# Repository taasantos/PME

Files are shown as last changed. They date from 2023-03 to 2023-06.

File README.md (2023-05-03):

# O meu repositório

## PME_5_ano - Dimensionamento de uma Ladder Hoist

### gear_defenition

Este ficheiro possui o código base para o dimensionamento de engrenagens.

**V3**

	- Equação dos módulos corrigida e módulos estão agora corretos

**V4**

	- Velocidades dos diferentes níveis corrigidaa
	- Alteração dos materiais para tentar manter os módulos abaixo de 6
	- Alteração do numero de dentes
	- Alteração do fator de condução
	- Acréscimo do cálculo do erro da velocidade de saida tendo em consideração a norma DIN 804

Estas alterações mudaram os valores todos das engrenagens e precisam de ser atualizados no relatório!!

**V5**

	- Alteração do diametro do tambor
	- Alteração da relação de transmissão o que altera o resto dos valores todos

**V6**

	- Alteração do diametro do tambor
	- Alteração dos angulos de engrenamento
	- Alteração do número de dentes
	- Alteração do módulo normalizado
	- Alteração do material da ultima engrenagem

---

Para verem os parametros das rodas e dos pinhões usar:

pinhao(nº de engrenamento)

roda(nº de engrenamento)

### problem_variables

Este ficheiro possui a defenição das variáveis do problema 

### gear_shafts

Este ficheiro possui o dimensionamento dos veios de transmisssão

**V2**

	- Calculo das forças de engrenamento
	- Calculo das forças exercidas nos veios
	- Dimensionamento do X0 Y0, X Y.
	- Cálculo dos Ps e c0 e c
	- Determinação dos rolamentos

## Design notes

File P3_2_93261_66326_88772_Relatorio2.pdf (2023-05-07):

# 2022/2023 Escada Elevatória Trabalho 2

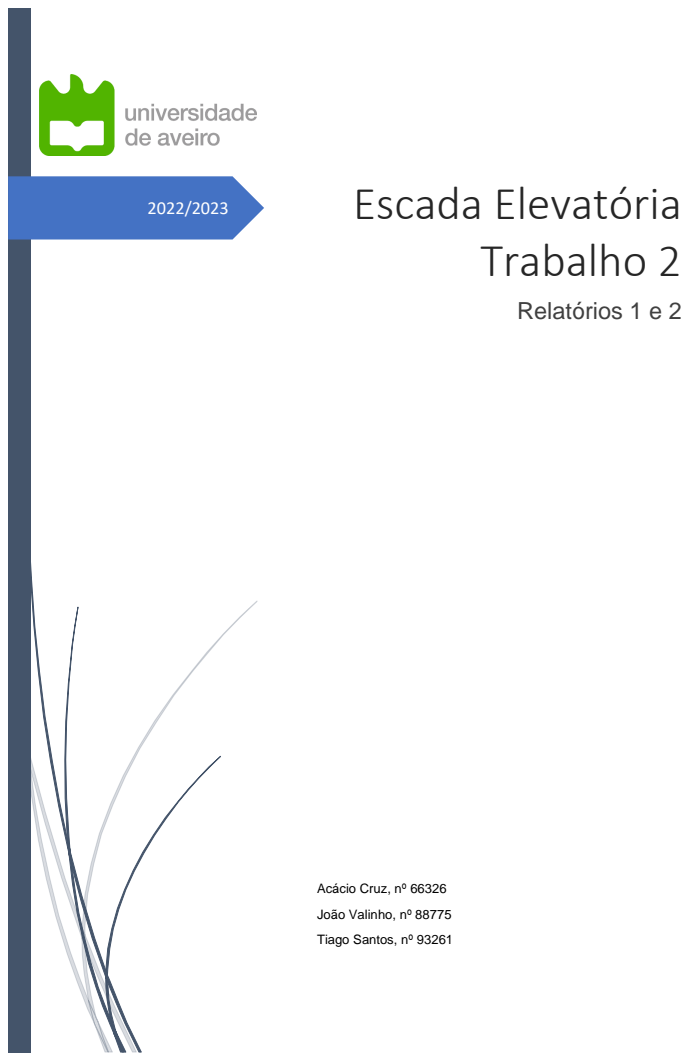
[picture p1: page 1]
Relatórios 1 e 2

Acácio Cruz, nº 66326

João Valinho, nº 88775

Tiago Santos, nº 93261

## Índice

Relatório 1

1. Introdução
1.1. Objetivo do projeto e enunciado
Uma escada elevatória é um mecanismo para transporte de carga de um nível de altura para outro. Ela é composta por uma plataforma elevatória montada em uma estrutura vertical que é acionada por um sistema elétrico. São geralmente usadas para fornecer acesso de materiais aos telhados de edifícios, movendo-se verticalmente ou numa inclinação.

O presente projeto visa, no âmbito da unidade curricular de Projeto de Máquinas e Estruturas, projetar uma escada elevatória para o transporte de painéis solares térmicos e fotovoltaicos a serem instalados em telhados. Assim sendo, inicialmente, traçar o sistema mecânico e elevatório. Consequentemente elevar o nosso conhecimento através da interligação de competências previamente adquiridas.

Será aplicado a este mecanismo, um redutor de velocidades proporcionando, assim, a diminuição da velocidade de um motor elétrico, mantendo a transmissão da potência constante de um motor, e aumento do binário, assegurando o transporte de painéis solares ao longo de uma escada elevatória.

Na primeira parte deste relatório, mostra-se um cronograma referente ao planeamento, apresenta-se o caderno de encargos do mecanismo a projetar e a análise a uma solução de mercado similar à do projeto em causa.

A seguir, é realizado uma descrição do mecanismo que a ser projetado, onde se indica os requisitos impostos de acordo com um enunciado e os que foram definidos pelos elementos do grupo imprescindíveis para o dimensionamento dos componentes mecânicos. Além disso, mostra-se a comparação de uma solução de mercado com uma aplicação similar à que se está a elaborar.

Posteriormente, é apresentado o método sequencial de todos os cálculos inerentes para dimensionar cada componente, compreendendo definições e condições teóricas e as relações de dependência entre a determinação das proporções de cada um, como por exemplo, os diâmetros do cabo e do tambor e das potências entre o redutor de velocidades (de eixos paralelos com veio de entrada e saída coaxiais, que inclui rodas dentadas helicoidais) e o motor que o aciona. Após cada componente dimensionado, mostra-se e discute-se os dados obtidos.

Por fim, expõe-se quer as considerações e verificações finais quer os valores obtidos mais relevantes a fim de se atingir o objetivo deste primeiro relatório.

1.2. Planeamento
Procurou-se reunir todos os membros do grupo semanalmente e em cada reunião, discutir as etapas do projeto de forma clara e específica. De modo a identificar os recursos, quer pessoais quer temporais, necessários para o cumprimento de cada tarefa, definiram-se áreas de especialização para cada elemento. Além disso, recorreu-se à criação de um cronograma detalhado (diagrama de Gantt) para o projeto, que inclui prazos e tarefas específicas para cada membro do grupo. Na figura 1, observa-se detalhadamente o trabalho desenvolvido ao longo das primeiras 5 semanas.

Figura 1 – Diagrama de Gantt.

2. Caderno de encargos do mecanismo
2.1. Descrição do mecanismo a projetar
O sistema mecânico é constituído por um motor freio acoplado a uma caixa redutora que inclui três pares de engrenagens de dentado helicoidal, para além de estar fixado a um tambor. Para o sistema elevatório, o cabo terá de ser capaz de efetuar a subida de cargas até à altura mencionada a seguir.

O dimensionamento destes componentes teve em conta os dados fornecidos pelo enunciado:

- Capacidade de carga/elevação: 250 kg;
- Área para elevação: 0,5 m x 1 m;
- Capacidade de elevação: 12 m;
- Velocidade de elevação: 35 m/min;

Além disso, considerou-se outros parâmetros e/ou características inerentes aos componentes projetados:

- Caixa redutoras de 3 velocidades para aplicar em elevação de carga;
- Estrutura dos grupos redutores é 2x1;
- Acionamento é feito por um motor freio;
- Par de engrenagens- 1º em aço de carbono C45, 2º em carbono temperado 33Mn5, 3º em aço ligado temperado 34NiCrMo6;
- Seleção de velocidade por um único manípulo;
- Potência de entrada – 1,39 kW;
- Velocidade de entrada – 1430 rpm;
- Velocidade de saída– 40,53 rpm.
3. Benchmarking – Easy Big WH-KI
O Easy Big WH-KI da GGR Group é um guindaste de escada projetado para transportar materiais de construção e equipamentos para um local de trabalho em alturas elevadas. Ele é montado em uma escada ou andaime, e o material ou equipamento é levantado por meio de uma polia conectada a um motor elétrico. Este produto é frequentemente usado em espaços de obras. [3]

Abaixo estão alguns pontos fortes e fracos do produto:

Pontos fortes:

- Fácil montagem e desmontagem.
Project Start Date | Display Week | 1
Project Name
| 13 | 14 | 15 | 16 | 17 | 18 | 19 | 20 | 21 | 22 | 23 | 24 | 25 | 26 | 27 | 28 | 1 | 2 | 3 | 4 | 5 | 6 | 7 | 8 | 9 | 10 | 11 | 12 | 13 | 14 | 15 | 16 | 17 | 18 | 19
WBS | TASK | LEAD | START | END | DAYS | %
DONE

WORK
DAYS | M | T | W | T | F | S | S | M | T | W | T | F | S | S | M | T | W | T | F | S | S | M | T | W | T | F | S | S | M | T | W | T | F | S | S
1 | Relatório 1 | - | -
1.1 | Marcação das reuniões semanais | Todos | sex 2/17/23 | sex 2/17/23 | 1 | 100% | 1
1.2 | Planificação das tarefas | Todos | sex 2/17/23 | sex 2/17/23 | 1 | 100% | 1
1.3 | Diagrama de Gantt | JV | sex 2/17/23 | dom 2/19/23 | 3 | 100% | 1
1.4 | Dimensionamento em Matlab | TS | sáb 2/18/23 | sex 3/10/23 | 21 | 100% | 15
1.4.1 | Criar Script de cálculo | TS | sáb 2/18/23 | qui 2/23/23 | 6 | 100% | 4
1.4.2 | Dimensionamento das
engrenagens
TS | sex 2/24/23 | qua 3/01/23 | 6 | 100% | 4
1.4.3 | Otimização das engrenagens | TS | sáb 3/04/23 | qua 3/08/23 | 5 | 100% | 3
1.4.4 | Verificações velocidades de saída | TS | qua 3/08/23 | qui 3/09/23 | 2 | 100% | 2
1.4.4 | Verificação da razão de condução | TS | qui 3/09/23 | sex 3/10/23 | 2 | 100% | 2
1.5 | Dimensionamento e seleção dos
restantes componentes | AC,JV | seg 2/20/23 | sex 3/10/23 | 19 | 100% | 15
1.5.1 | Cabo | AC,JV | seg 2/20/23 | sáb 2/25/23 | 6 | 100% | 5
1.5.2 | Tambor | AC,JV | sáb 2/25/23 | qui 3/02/23 | 6 | 100% | 4
1.5.3 | Motor | AC,JV | sex 3/03/23 | dom 3/05/23 | 3 | 100% | 1
1.5.4 | Verifcação e correção dos
cálculos | AC,JV | sex 3/03/23 | sex 3/10/23 | 8 | 100% | 6
1.6 | Desenho esquemas cinemáticos | AC | qua 3/01/23 | seg 3/13/23 | 13 | 100% | 9
1.6.1 | Realização do esboço
cinemático | AC | sex 3/03/23 | sáb 3/04/23 | 2 | 100% | 1
1.6.2 | Realização do esquema
cinemático final | AC | dom 3/12/23 | seg 3/13/23 | 2 | 100% | 1
1.7 | Produção do Relatório | JV | sex 3/03/23 | sex 3/17/23 | 15 | 100% | 11
1.7.1 | Criação da estrutura do
documento | JV | sex 3/03/23 | dom 3/05/23 | 3 | 100% | 1
1.7.2 | Escrita do documento | Todos | dom 3/05/23 | sex 3/17/23 | 13 | 100% | 10

Week 4

6 mar 2023 | 13 mar 2023 Week 5
Ladder Hoist
2/17/2023 (sexta-feira) | Semana 1 | Semana 2
| 13 fev 2023 | 20 fev 2023

Semana 3
27 fev 2023

- Capacidade máxima de carga de 250 kg.
- Possibilidade de elevação de materiais até 24 metros de altura, com articulação.
- Velocidade de elevação ajustável.
- Sistema de freio automático de segurança.
- Adequado para locais de construção em áreas urbanas onde o espaço é limitado e não é possível usar guindastes maiores.
- Redução dos riscos de lesões nos trabalhadores que realizam a elevação manual de materiais.

Pontos fracos:

- Capacidade limitada de carga em comparação com guindastes maiores.
- A mobilidade é restrita a locais onde uma escada ou andaime podem ser utilizados para a sua instalação.
- A operação do guindaste requer treinamento e habilidade para garantir a segurança dos trabalhadores e evitar danos aos materiais ou equipamentos transportados.
- Custo de aluguer ou compra pode ser maior do que o de outras soluções de elevação de materiais.

Em resumo, o Easy Big WH-KI pode ser uma opção eficiente e segura para a elevação de materiais em locais de construção em áreas urbanas ou onde não é possível usar guindastes maiores, desde que seja operado adequadamente e respeitando as suas limitações de carga e mobilidade.

Em comparação com esse produto concorrente, o mecanismo projetado tem uma capacidade máxima de carga semelhante, mas uma altura máxima de elevação menor.

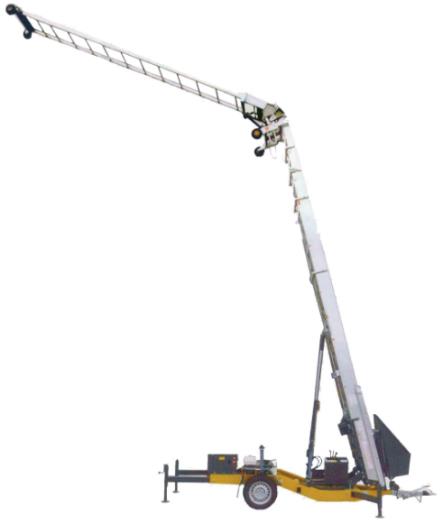
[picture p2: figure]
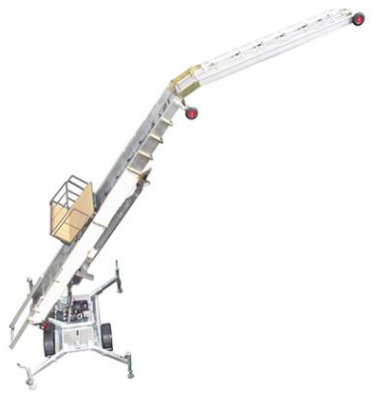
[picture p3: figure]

4. Dimensionamento e seleção dos componentes mecânicos
4.1. Cabo
O primeiro componente a ser dimensionado foi o cabo de aço. As classes e tipos de cabos de aço selecionados para o estudo serão apresentados na tabela 1, juntamente com as características imprescindíveis para os cálculos retiradas de [2].

A fim de se aumentar o tempo de vida deste componente e este não se romper, utilizou-se um fator de segurança (fs) de 5 para guinchos, de acordo com a tabela 6.27 de [2].

Figura 2 – Imagem ilustrativa do Easy Big WH-KI.

Tabela 1 – Exemplos cabos de aço

Tipo | Classe | Fator de contrução (f) | Fator para diâmetro mínimo/recomendado do tambor (ft) | Carga de rutura mínima [kN] | Tensão de rotura [MPa]
1x7 | Cordão | 0,596 | - | 13,7 | 1570
1x19 | | 0,58 | - | 13,2
6x19 | Seale | 0,395 | 34/51 | 27 | 1770
6x25 | Filler, WS | 0,405 | 26/39 | 41
6x36 | | | 23/35 | 35,7 (1*) | -

1* - O valor de carga de rutura mínima foi pesquisado em [2].

Primeiramente, definiu-se o comprimento do cabo através da equação (1), sendo a altura máxima 12 metros.

Lc = 2 × Hmáx
(1)
Lc = 2 × 12 = 24
- Lc – comprimento do cabo [m]
- Hmáx – altura máxima [m]

Adicionou-se 2 metros ao comprimento final, obtendo-se então 26 metros de comprimento do cabo, visto que o diâmetro do tambor é 0,305 metros, conta-se com mais 2 polias do mesmo diâmetro, o que perfaz um aumento de 1,9 metros, aproximadamente.
De seguida, procedeu-se à determinação da área transversal do cabo e do peso carga que o cabo tem de suportar, desprezando as forças de atrito, a partir das equações (2) e (3), respetivamente. Assim, a expressão (4) calcula a pressão nessa área. Os valores apresentados referem-se ao cabo que foi escolhido, sublinhado a verde, ou seja, para os outros cabos aplicou-se o mesmo procedimento.

Ac =

Øc

2 × π
4 | (2)

Ac =

0,008 ² × π
4

= 5,027 ∗ 10⁻⁵

- Ac – área transversal do cabo [m² ]
- Øc – diâmetro do cabo [m]
F = m × g | (3)

P = 250 × 9,81 = 2452,50

- F – força aplicada ao cabo [N]
- g – constante gravitacional = 9,81 [m/s² ]
- m – massa da carga [kg]

σ =

F
Ac | (4)

σ =

2452,50
5,027 ∗ 10⁻⁵ = 49 Mpa

- F – força aplicada ao cabo [N]
- Ac – área transversal do cabo [m²
]
- σ – tensão axial no cabo [MPa]

Depois, mediu-se a deformação elástica do cabo pela lei de Hooke com a equação (5). A área metálica efetiva do cabo foi estimada com recorrendo à equação (6), sendo o módulo de Young para cabos de aço é 200 GPa.

ΔL =

F × L
Am × E | (5)

ΔL =

2452,5 × 26
9,50 × 10⁻⁶ × 200 × 10⁹ = 0,17 m
- F – força aplicada ao cabo [N]
- Am – área metálica efetiva do cabo [m² ]
- ∆L– alongamento do cabo [m]
- E – módulo de elasticidade [GPa]
- Lc – comprimento do cabo [m]

Am = f × Øc

2 | (6)

Am = 0,38 × 0,005² = 9,56 × 10⁻⁶ m²

- Am – área metálica efetiva do cabo [m² ]
- Øc – diâmetro do cabo [m]
- f - fator de construção [adimensional]

Por fim, aplicando a equação (7), determinou-se os valores mínimo e recomendado para o diâmetro do tambor, deve estar preferencialmente compreendido no intervalo [0,238; 0,476] metros. Deste modo, é permitido fazer a comparação dos resultados obtidos para cada um dos cabos na tabela 2.

Øt = ft × Øc | (7)

Øt,mín = 42 × 0,005 = 0,21 m

Øt,rec = 72 × 0,014 = 0,36 m

- Øt – diâmetro do tambor [m]
- Øc – diâmetro do cabo [m]
- ft – Fator para o diâmetro mínimo/recomendado do tambor [adimensional]

Tabela 2 - Valores obtidos para selecionar o cabo.

Após o seu dimensionamento, o cabo selecionado é do tipo 6x7, da classe CF, fornecido pela Luiz Godinho. [3]

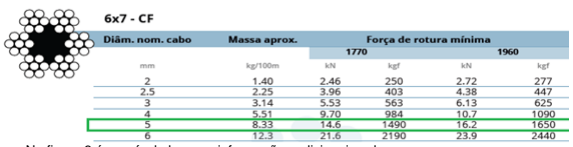
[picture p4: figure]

Na figura 3 é possível observar informações adicionais sobre o mesmo.

4.2. Tambor
A partir da determinação do comprimento do cabo, pode-se utilizar esse valor para calcular o número de voltas do tambor, mas antes deve-se obter o seu perímetro, recorrendo aos valores dos diâmetros recomendado e mínimo, através das equações (8) e (9).
Pt = Øt × π | (8)

Pt,d rec = 0,36 × π = 1,13 m

Pt,d mín = 0,21 × π = 0,659 m

- Pt –perímetro do tambor [m]
- Øt – diâmetro do tambor [m]

Nvoltas =

Lc
Pt

(9)

Nvoltas,d rec =

26
1,13 = 23

Nvoltas,d mín =

26
0,659 = 39
- Nvoltas – número de voltas [adimensional]
- Pt –perímetro do tambor [m]
- Lc – comprimento do cabo [m]

Posteriormente, fez-se uma pesquisa em [4], e acrescentou-se o cálculo dos valores necessários para o dimensionamento do tambor.
Deste modo, determinou-se 4 parâmetros da ranhura do cabo que permitem definir o comprimento do tambor, sendo mencionados a seguir, bem como se apresenta as respetivas equações (10 a 13). Os resultados obtidos podem ser observados na tabela 3, tal como na figura 4 está ilustrado o desenho técnico de um tambor com esses parâmetros.
A = 1,08 × Øc | (10)

A = 1,08 × 0,005 = 0,0054 m

B = 1,06 × Øc | (11)

B = 1,06 × 0,005 = 0,0053 m

C = 0,3 × Øc | (12)

C = 0,3 × 0,005 = 0,0015 m

R = 0,15 × Øc | (13)

R = 0,15 × 0,005 = 0,00075 m

- A – elevação da ranhura [m]
- B – diâmetro da ranhura [m]
- C – profundidade da ranhura [m]
- D – raio superior [m]
- Øc – diâmetro do cabo [m]

Tabela 3 - Parâmetros associados às ranhuras do cabo.

Parâmetros | Resultado | Unidades
A | 0,005 | m
B | 0,005 | m
C | 0,002 | m
R | 0,001 | m

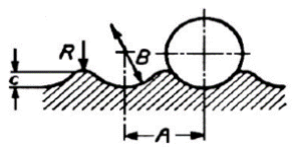
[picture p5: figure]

Após o cálculo da elevação da ranhura (A), deu-se o cálculo do comprimento do tambor através da equação (14). Os valores obtidos para o comprimento do tambor mínimo e recomendado foi 0,24 e 0,35 metros, respetivamente. A figura 5 mostra qual a dimensão do tambor que está a ser determinada.

Lt = (Nvoltas × A)+ Øc
(14)

Lt,d rec = (23 × 0,005) + 0,005 = 0,12

Lt,d mín = (39 × 0,005) + 0,005 = 0,20

- A – elevação da ranhura [m]
- Nvoltas – número de voltas [adimensional]
- Lt – comprimento do tambor [m]
- Øc – diâmetro do cabo [m]

Figura 3 – Localização dos parâmetros A, B, C, D associados à ranhura do cabo num desenho técnico.

Figura 4 – Visualização do comprimento do tambor.

Por fim, determinou-se a distância mínima entre o tambor e a roldana. Tendo em conta que o nosso cabo tem ranhuras, recorreu-se à equação (15), previamente definida, para se obter essa distância.

O ângulo de desvio de cabos de aço (β) é 2°.

O resultado obtido para os comprimentos do tambor mínimo e recomendado foram 5,3 metros e 3,6 metros, respetivamente. Verifica-se na figura 6 um desenho representativo do mesmo.

Lmín = 15 × Lt
(15)

Lmín,d rec = 15 × 0,12 = 1,8

Lmín,d mín = 15 × 0,20 = 3

- Lmín– distância mínima entre o tambor e a polia [m]
- Lt – comprimento do tambor [m]

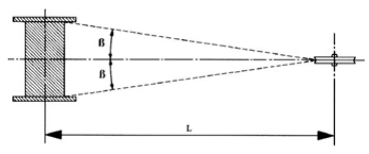
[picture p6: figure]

No seguimento das necessidades encontradas, no mercado propõe-se a seguinte solução na Tabela 4, cujo fornecedor é a Eletrolift. [5]

Tabela 4 – Comparação entre os valores obtidos e os do tambor.

Øt [m] | Pt [m] | Nvoltas | Lt [m] | Lmín [m]
Intervalo aceitável | [0,21; 0,36] | [1,13; 0,659] | [23; 39] | [0,12; 0,20] | [1,8; 3]
Modelo M-303-P2 | 0,3048 | 0,958 | 23 | 0,22 | 3,2
4.3. Motor
As características que se teve em conta para a seleção do motor foram este ser elétrico, a sua potência e a sua velocidade de rotação.

Deste modo, seguiu-se o seguinte procedimento de cálculo: força aplicada (Peso) quando a escada é vertical e o torque do motor quando a distância do eixo do tambor é igual ao seu raio (metade do diâmetro), recorrendo às equações (3) e (16).

τm = F ×

∅t
2

(16)

Tm = 2452,5 ×

0,360
2

= 441,45

- F– força aplicada ao cabo [m]
- Øt – diâmetro do tambor [m]
- Τm – torque do motor [Nm]

Após o cálculo do torque, obteve-se o valor da velocidade de saída do redutor com o intuito de definir a potência do motor, recorrendo às equações (17) e (18). Considerou-se a velocidade de elevação igual a 35 m/min, isto é, 0,583 m/s, aproximadamente.

Figura 6 – Distância entre o tambor e a polia e o ângulo de desvio de cabos de aço.

- ωsaída − velocidade de saída do redutor [rpm]
- velev – velocidade de elevação [m/s]
- Øt – diâmetro do tambor [m]
- ωsaída − velocidade de saída do redutor [rpm]
- P – potência do motor [kW]
- Τm – torque do motor [Nm]

Assim sendo, escolheu-se um trifásico IEC com freio DC fabricado pela Bernati, da série BCL. Algumas das características adicionais são as seguintes: [6]

- Potência do motor: 1,5 kW;
- Velocidade de rotação: 1500 rpm;
- Frequência (f): 50 Hz;
- 4 pólos;
- IP65: proteção total contra poeiras e contra jatos de água.

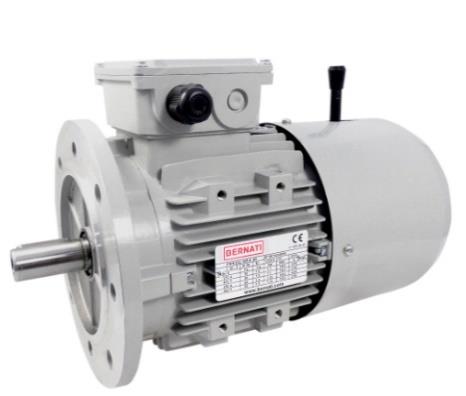
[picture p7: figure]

Figura 7 – Imagem do motor freio selecionado.

4.4. Engrenagens
4.4.1. Determinação do número de andares

Com a velocidade de saída do redutor determinada, estabeleceu-se o número de andares que o redutor terá, recorrendo à equação (19). Obteve-se um valor de 2,77, ou seja, 3 andares.

Nandares =

log10 (

ωentrada
ωsaída

)

log10(4)

(19)

Nandares =

log10 (

1430
30,93)

log10(4)

= 2,77 ≅ 3

- Nandares − número de andares [adimensional]
- ωentrada – velocidade de entrada [rpm]
- ωsaída − velocidade de saída do redutor [rpm]

ωsaída =

velev × 60
π × ∅t

(17)

ωsaída =

0,583 × 60
π × 0,360 = 30,93

P =

2 × π × Tm × ωsaída
60 × 1000

(18)

P =

2 × π × 441,45 × 30,93
60 × 1000 | = 1,43

4.4.2. Determinação da relação de transmissão total
De seguida, obteve-se a relação de transmissão total através da equação (20), sendo esta a razão entre a velocidades de entrada e de saída. Chegou-se a 46,23, cujo valor resulta da relação de transmissão de cada engrenagem através da equação (21). Deste modo, obtém-se as relações de 4:1, 4:1, 2,5:1 referente aos andares 1, 2 e 3, respetivamente.

Utotal =

ωentrada

ωsaída | (20)

Utotal =

1430
30,93 = 46,23

Utotal real = u1

. u2

. u3
(21)

Utotal real = 4 ∗ 4 ∗ 2,5 = 40

Utotal – relação de transmissão total [adimensional]
Utotal real – relação de transmissão total real [adimensional]
•u1 − relação de transmissão do primeiro andar [adimensional]
•u2 − relação de transmissão do segundo andar [adimensional]
•u3 − relação de transmissão do terceiro andar [adimensional]

Os resultados da transmissão total são idênticos, então pode-se afirmar que os valores atribuídos para a relação de transmissão de cada andar são aceitáveis.

4.4.3. Determinação do número de dentes
Definiu-se o número de dentes (Z) do pinhão recorrendo à equação (22), sendo que o valor do ângulo αt determinado a partir do ângulo de pressão α (este cálculo será apresentado mais tarde no subcapítulo 4.4.5) e o de β admitido inicialmente como 20°. O valor escolhido poderá ser arbitrário desde que cumpra a condição de que o número destes seja superior ou igual a 15.

Zpinℎão ≥

2 × cos β
(sin αt

)

2

(22)

Zpinℎão ≥

2 × cos(20)
(sin(21,17))

2 = 14,41 ≅ 15

•Zpinhão – número de dentes do pinhão [adimensional]
•β − ângulo de hélice primitiva do dentado [°]
•αt − ângulo de pressão aparente [°]

Com base nas relações de transmissão de cada andar e no número de dentes do pinhão, obteve-se o número de dentes da roda através da relação apresentada pela equação (23). Os valores obtidos foram sendo alterados com o decorrer das iterações com o intuito de determinar um módulo mais eficiente para que o redutor fique o mais compacto possível. O valor do número de dentes pode ser visualizado na Tabela 5.

u =

Zroda

Zpinℎão

≡ Zroda = Zpinℎão × u | (23)

Zroda,1 = Zpinℎão,1 × u1 = 17 × 4 = 68

Zroda,2 = Zpinℎão,2 × u2 = 19 × 4 = 76

Zroda,3 = Zpinℎão,3 × u3 = 25 × 2,5 = 63

- u – relação de transmissão [adimensional] •Zpinhão – número de dentes do pinhão [adimensional] •Zroda – número de dentes da roda [adimensional]

Tabela 5 - Número de dentes das engrenagens.

Nível da engrenagem | Pinhão | Roda
1 | Z1 = 17 | Z2 =68
2 | Z3 = 19 | Z4 =76
3 | Z5 = 25 | Z6 = 63
4.4.4. Determinação dos módulos
Após a obtenção dos dentes de cada roda dentada, procedeu-se ao cálculo do módulo da engrenagem. Foi dimensionado utilizando dois métodos: a rutura de em flexão do dente e a fadiga por ação de tensões de contacto durante o engrenamento, ou seja, as tensões de Hertz, sendo que será selecionado o maior valor obtido entre ambos os métodos. Este irá corresponder aos critérios de segurança impostos por cada um deles.

Para isso, foi necessário o cálculo dos parâmetros expressos nas equações de cada um dos métodos. Pode ser observado na Tabela 6 os resultados obtidos arredondados a 4 casas decimais bem como as informações relevantes para a compreensão dos mesmos. É de salientar que foram utilizados aços para a constituição das engrenagens. Para o nível 1 (Z1+Z2) foi escolhido o de carbono C45, para os níveis 2 (Z3+Z4) e 3 (Z5+Z6) foram selecionados o carbono temperado (óleo) 33Mn5. Ao escolher este material, os valores assumidos para os módulos de elasticidade (E) e para os coeficientes de Poisson caracterizam cada liga de aço.

Tabela 6 - Parâmetros necessários ao cálculo dos módulos.

Parâmetro | Símbolo | Expressão | Resultado | Observação
Fator proporcional largura/módulo | CLβ | (CL = L / mn) | 10 | 1* β1 = 20º β2 = 35º β3 = 40º
| | CLβ = CL / cosβ | CLβ,1 = 10,6418 CLβ,2 = 12,2077 CLβ,3 = 13,0541
Fator de efeito do dentado helicoidal | Yβ | Yβ = 1 / cosβ | Yβ,1 = 1,0642 Yβ,2 = 1,2208 Yβ,3 = 1,3054
Fator de efeito dinâmico | KM | - | 1 | 2*
Fator de duração | KbL | KbL = log10(NLh) / 8 | KbL,1 = 1,1543 KbL,2 = KbL,3 = 1,0791 | 3*
tensão de contacto Fator de fadiga à | KHL | KHL = 8 / log10(NLh) | KHL,1 = 0,8663 KHL,2 = KHL,3 = 0,9267 | 3*
Fator de alinhamento | KA | KA = 1 se L / d1 <1 | 1 | L/d1<1
Fator de condução | Yε | Yε = 1/ ε | Yε,1= 0,6569 Yε,2= 0,8 Yε,3= 0,8 | Calculado a seguir. 4*
Fator de concentração de tensões | YF | YF = 0,4 se x = 0 | 0,4 | Correção do dentado (x) é igual a 0. 5*

Módulo de elasticidade | E | - | E1 =200 GPa E2=E3=210 GPa | Módulos para liga utilizada.
Coeficiente de Poisson | v | - | 0,3 | Coeficiente para cada liga
Rotação do primeiro pinhão | n1 | - | 1430 rpm | Valor do catálogo 6*

1* - Valor de CL retirado da tabela 4.7 de [2], porque potência é maior que 10 kW e são rodas helicoidais, optou-se pelo valor de 10.

2* - Valor de KM retirado da tabela 4.5 de [2], optando-se pela entrada (máquina motriz) e saída (máquina acionada) em movimento uniforme.

3* - Número de ciclos de cada pinhão:

- NLh (1) = 20 anos * 250 dias * 8 horas * 60 minutos * n1 = 1,7160*10⁹
- NLh (3) = 20 anos * 250 dias * 8 horas * 60 minutos * n1 / u1 = 4,2900*10⁸
- NLh (5) = 20 anos * 250 dias * 8 horas * 60 minutos n1 / u2 = 4,2900*10⁸

4 *- A razão de condução (ε) teve de ser calculada, pois Z1 < 19. A sua equação é

ε =

1
πmt cos αt

[√Re1
2 −Rb1

2 + √Re2
2 − Rb2

2 − e sin αt

]+
L tan β
πmt

sendo Re e Rb o raio externo e o raio da base do pinhão ou roda, por essa ordem. O resultado obtido para o nível 1 de engrenagem é ε1= 1,5222. Para os outros níveis utilizou-se o valor admitido.

5 *- Valor assumido inicialmente. Após o cálculo do módulo, como no grupo redutor base, o número de dentes do par é 17/68 e assume o mesmo valor de 4 mm, não será necessário realizar a correção de dentado.

6* - Valor retirado do catálogo [7].

Depois de determinar as incógnitas necessárias, recorreu-se às equações (25) e 26) para calcular o módulo à rotura de fadiga em flexão do dente e à fadiga por ações de tensões de contacto (tensões de Hertz), respetivamente. Os resultados obtidos estão presentes na tabela 7.

- mn – módulo real da engrenagem [mm]
- P – potência a transmitir pela engrenagem do catálogo [W]

mn ≥ √
1,96 × 10⁴ × P × cos β × KM × KbL × Yε

CLβ × σb,Limite × n1 × KA × ZV1 × YF × Yβ

× (

u + 1
u

)
3
(25)

mn1 ≥ √
1,96 × 10⁴ × 1500 × cos(20) × 1 × 1,1543 × 0,6569 10,6418 × 240 × 1430 × 1 × 20,4876 × 0,4 × 1,0642

× (

5
4

)

3
= 0,8513

mn2 ≥ √
1,96 × 10⁴ × 1500 × cos(35) × 1 × 1,0792 × 0,8 12,2077 × 285 × 357,5 × 1 × 34,5669 × 0,4 × 1,2208

× (

5
4

)

3
= 1,0206

mn3 ≥ √
1,96 × 10⁴ × 1500 × cos(40) × 1 × 1,0792 × 0,8 13,0541 × 285 × 89,375 × 1 × 55,6132 × 0,4 × 1,0354 × (

3,5
2,5

)

3
= 1,3427

- σb,Limite – tensão limite de fadiga à flexão [MPa]
- u – razão de transmissão [adimensional]
- CLβ – fator proporção largura / módulo [adimensional]
- n1 – rotação do pinhão [rpm]
- Zv1 – número de dentes virtual do pinhão [adimensional]
- KM – fator de efeito dinâmico [adimensional]
- KA − fator de alinhamento [adimensional]
- KbL− fator de fadiga por flexão [adimensional]
- Yε – fator de condução [adimensional]
•YF − fator de concentração de tensões à flexão [adimensional]
- Yβ − fator de efeito do dentado helicoidal [adimensional]
- β − ângulo de hélice primitiva do dentado [º]

mn ≥ √
6 × 10⁴ × P × cos β × KM
π

2 × CLβ × σH,Lim

2 × n1 × KA × ZV1 × KHL × sin(2α)

×

2 × E
(1 − v

2)

× (

u +1
u

)
3
(26)

mn1 ≥ √
6 × 10⁴ × 1500 × cos(20) × 1 π

2 × 10,6418 × 500² × 1430 × 1 × 20,4876 × 0,8663 × sin(2 × 20)

×

2 × 200 × 10⁹
(1 − 0,3

2)

× (

5
4

)

3
= 4,7692

mn2 ≥ √
6 × 10⁴ × 1500 × cos(35) × 1 π

2 × 12,2077 × 745² × 357,500 × 1 × 34,5669 × 0,9267 × sin(2 × 20)

×

2 × 210 × 10⁹
(1 − 0,3

2)

× (

5
4

)

3
= 4,4209

mn3 ≥ √
6 × 10⁴ × 1500 × cos(40) × 1 π

2 × 13,0541 × 745² × 89,375 × 1 × 55,6132 × 0,9267 × sin(2 × 20)

×

2 × 210 × 10⁹
(1 − 0,3

2)

× (

3,5
2,5

)

3
= 5,9477
- mn – módulo real da engrenagem [mm]
- P – potência a transmitir pela engrenagem do catálogo [W]
- u – razão de transmissão [adimensional]
- CLβ – fator proporção largura / módulo [adimensional]
- n1 – rotação do pinhão [rpm]
- Zv1 – número de dentes virtual do pinhão [adimensional]
- KM – fator de efeito dinâmico [adimensional]
- KA − fator de alinhamento [adimensional]
- Yβ − fator de efeito do dentado helicoidal [adimensional]
- β − ângulo de hélice primitiva do dentado [º]
- σH,Lim – tensão limite de fadiga de contacto [MPa]
- KHL− fator de fadiga à tensão de contacto [adimensional]
- α − ângulo de pressão [º]
- E – módulo de elasticidade [MPa]
- v – coeficiente de Poisson [adimensional]

Tabela 7 - Módulos da fadiga em flexão e da fadiga em contacto obtidos.

mn u | módulo da fadiga em flexão [mm] | módulo normalizado [mm] | módulo da fadiga em contacto [mm] | módulo normalizado [mm] | módulo final [mm]
u1 | 0,8513 | 1,00 | 4,7692 | 5,0 | 5,0
u2 | 1,0206 | 1,25 | 4,4209 | 4,5 | 4,5
u3 | 1,3427 | 1,50 | 5,9477 | 6,0 | 6,0

4.4.5. Parâmetros geométricos associados ao dentado helicoidal
Com os valores do módulo das engrenagens determinados, sucedeu-se o cálculo dos parâmetros finais das mesmas. Na tabela 8, pode-se consultar quais as expressões usadas para calcular os parâmetros. Os resultados obtidos podem ser verificados na tabela 9.

Tabela 8 - Tabela retirada de [1], com os parâmetros geométricos referentes ao dentado helicoidal.

Parâmetro | Símbolo | Expressão | Unidades
Módulo aparente | mt | mt = mn /cosβ | mm
Passo | p | p = mn · π | mm
Passo aparente | pt | pt = mt · π | mm
Ângulo de pressão nominal | α | 20° | °
Ângulo de pressão aparente | αt | tanαt = tanα / cosβ | °
Diâmetro primitivo | D | D = mn · Z | mm
Diâmetro de base | Db | Db = D · cosα | mm
Ângulo de dentado | β | β = [0°,5°,10°,15°,20°,25°,30°,35°,40°,45°] | °
Número de dentes | Z | Atribuído | adimensional
Número de dentes virtual | Zv | Zv = Z / cos³β | adimensional
Largura da roda | L | a ser dimensionado ou adotado | mm
Largura do dentado | Lt | Lt = L / cosβ | mm
Diâmetro do pé de dente | Dp | Dp = D – 2 · hf | mm
Diâmetro externo (cabeça) | De | De = D + 2 · mn | mm
Altura total do dente | hz | hz = 2,25 · mn | mm
Altura cabeça do dente | hc | hc = mn | mm
Altura do pé do dente | hf | hf = 1,25·mn | mm
Folga da cabeça | s | s = 0,25*mn | mm
Razão de transmissão | u | u = Z2 / Z1 = D2 / D1 = n1 / n2 | adimensional
Entre eixo | e | e = [(Z2+Z1) / 2] · mt | mm

Como no grupo redutor base, o número de dentes entre os pares é 17/68 e assumem o mesmo módulo de 4 mm, não será necessário realizar a correção de dentado.

Tabela 9 - Resultados obtidos para os parâmetros geométricos referentes ao dentado helicoidal.

Parâmetros | u1 | u2 | u3
mt | 5,32 | 5,49 | 7,83
p | 15,71 | 14,14 | 18,85
pt | 16,72 | 17,26 | 24,61
α | 20 | 20 | 20
αt | 21,17 | 23,96 | 25,42
D (pinhão/roda) | 90,46 / 361,82 | 104,38 / 417,51 | 195,81 / 493,44
Db (pinhão/roda) | 84,35 / 337,40 | 95,38 / 381,54 | 176,86 /445,69
β | 20 | 20 | 20
Z (pinhão/roda) | 17 / 68 | 19 / 76 | 25 / 63

ZV (pinhão/roda) | 20,49 / 81,95 | 34,57 / 138,27 | 55,61 / 140,15
L | 35 | 60 | 35
Lt | 37,24 | 73,24 | 45,68
Dp (pinhão/roda) | 77,96 / 349,32 | 93,13 / 406,25 | 180,81 / 478,44
De (pinhão/roda) | 100,46 / 371,82 | 113,37 / 426,50 | 207,81 / 505,44
hz | 11,25 | 10,125 | 13,5
hc | 5,00 | 4,50 | 6,00
hf | 6,25 | 5,625 | 7,50
s | 1,25 | 1,125 | 1,50
u | 4 | 4 | 2,5
e | 226,14 | 260,94 | 344,63
5. Evolução do esquema cinemático do sistema mecânico
Inicialmente, esboçou-se o esquema cinemático de modo a ter uma visualização da configuração do interior do redutor a ser dimensionado, ilustrando o pensamento da separação dos pares de engrenagens ao longo dos níveis, como se pode observar na figura 8.

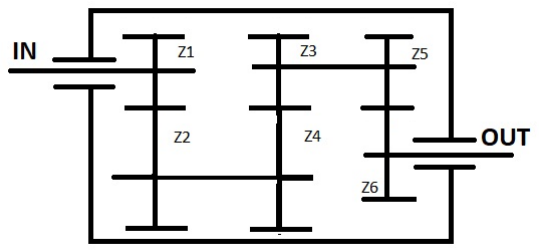
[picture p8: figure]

Figura 8 - Esboço do esquema cinemático.

Após o cálculo de todos os parâmetros necessários, desenhou-se o esquema cinemático do redutor com o intuito de avaliar se não haveria interceção entre engrenagens e veios ou erros na arquitetura do mesmo.

É de salientar que a escolha desta arquitetura para o redutor tem como principal objetivo a otimização do espaço presente na base da escada.

Pode ver-se o resultado do esquema cinemático, através da figura 8.

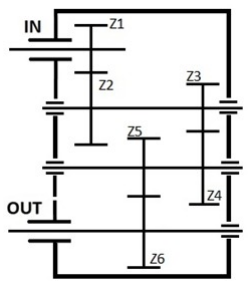
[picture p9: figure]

Figura 9 - Esquema cinemático final.

6. Conclusão
Este relatório está divido em diferentes etapas, e todas elas com o seu peso relativo para obtenção da solução para o problema proposto.

Na primeira etapa realizamos uma pesquisa de várias soluções, todas elas com diferentes tipos de estratégia para o mesmo tipo de problema. Optamos por escolher a opção apresentada acima neste relatório, porque inferimos ser o mais semelhante em características técnicas à nossa necessidade e com a maior diversidade de soluções para possíveis controvérsias.

Posto isto, a etapa seguinte é basicamente cálculos, ou seja, forças e cargas, dimensionamento do cabo de aço, motor elétrico, tambor para o cabo de aço e caixa-redutora (engrenagens).

Para o nosso cabo de aço, escolhemos um 6x25 Filler com um diâmetro 0,008 m que é utilizado para este tipo de trabalhos com uma enorme capacidade de resistência à rutura e fadiga, consequentemente dimensionamos um tambor onde se irá enrolar o cabo selecionado. Como se trata de uma carga já consideravelmente alta optamos por um tambor com nervuras. Pelos nossos cálculos e para os requisitos exigidos o tambor deveria ter um diâmetro de 0,31 m com a capacidade para 27 voltas com nervuras, assim sendo com estes valores obtidos e considerando os valores aconselhados fomos ao mercado e escolhemos um tambor de diâmetro 0,30 m com capacidade para 35 voltas. No seguimento deste processo necessitamos de selecionar o equipamento que irá fornecer potência ao nosso sistema, o motor elétrico, sabendo a carga que irá ser movimentada e velocidade de movimentação da mesma. Após a realização de uma pesquisa optamos por um motor elétrico com freio DC de 1,5kw com 1500 rpm. Este motor tem um freio eletromagnético que para este tipo de trabalhos tem um papel de elevada importância que consiste no travamento do cabo impedindo que o mesmo se mova quando o motor não é ativado.

Por fim, a última etapa neste relatório é o dimensionamento da caixa redutora, pela análise e cálculos feitos a nossa caixa irá ter 3 andares, com 3 pares pinhão – roda, isto é, a nível de dentes Z1 tem 17 dentes, Z2 tem 68, Z3 tem 17, Z4 tem 68, Z5 tem 26 e por fim Z6 tem 58 dentes. Cada par tem uma relação de 4:1, 4:1 e 2,5:1 respetivamente. Apesar de terem sido selecionados estas relações de transmissão, a relação total desejada não coincide com a real. A norma DIN 804 assume para estes casos que o erro associado das velocidades de saída deve estar compreendido entre -2% e 3%. O erro obtido no caso dimensionado foi de 0.63%, respeitando assim a norma e não sendo necessário alterar as relações de transmissão. Este erro foi calculado através da fórmula do erro relativo.

Em geral, os objetivos principais previstos para este relatório foram cumpridos. É importante salientar ainda que o material usado no último par de engrenagem (34NiCrMo6) é um material caro e difícil de fabricar sendo que mais à frente é necessário otimizar este par de modo a poder ser selecionado um material mais economicamente favorável mantendo o módulo inferior ou igual a 6.

Os valores gerais das engrenagens, no entanto, serão possivelmente alvo de alterações durante o processo de dimensionamento dos veios para cada roda dentada.

Relatório 2

1. Introdução
De modo a continuar com o dimensionamento do redutor, procedeu-se ao dimensionamento de rolamentos e de veios a utilizar, de modo a garantir a integridade estrutural do redutor e a sua funcionalidade.

Começou-se por identificar e calcular as forças aplicadas nos pares pinhão/roda e consequentemente nos veios dos mesmos, representando-as em esquemas.

De seguida determinou-se as reações presentes nos apoios dos veios sendo que se foram considerados 2 planos possíveis: OXY e OXZ. O cálculo destas reações foi feito através de um software chamado FTool. Este software apresenta cálculos precisos sobre o comportamento dos veios e inclusive permite uma boa organização no que toca à representação e armazenamento das forças para testes futuros.

Após termos as reações nos apoios, foi possível determinar as forças radiais e axiais aplicadas em cada rolamento sendo que com estas se procedeu ao cálculo dos fatores de carga C e C0, permitindo-nos escolher os rolamentos a usar, a partir dos catálogos dos fabricantes.

Através dos critérios de cedência (Tresca e Von Mises) e dos momentos fletor máximo e torsor, calculou-se o diâmetro mínimo para um fator de segurança de 1,5 que é comum no fabrico de redutores. Em função deste diâmetro procedeu-se então ao cálculo da flecha na zona de engrenamento e da rotação nos apoios dos veios usando também o software FTool.

Com estes valores, procedeu-se ao dimensionamento das chavetas e/ou veios estriados de modo que as engrenagens possam transmitir o momento torsor ao veio. No caso deste projeto foram dimensionadas chavetas para todos os veios e veio estriado para o lado direito do segundo veio.

Por fim, fez-se um esboço de cada veio e realizou-se o dimensionamento à fadiga para cada uma das secções de transição geométrica do mesmo.

2. Identificação das forças de engrenamento aplicadas nos veios
Como se pode observar no esquema cinemático do relatório 1, o redutor irá possuir 4 veios sendo que estes precisam de ser dimensionados tendo em conta os esforços exercidos nos mesmos, essencialmente pelas forças de engrenamento. Que podem ser caracterizadas por três: força tangencial, força radial e força axial. As fórmulas para calcular cada uma delas estão representadas pelas equações (27) a (31), cujos resultados, para cada par pinhão/roda, são apresentados juntamente com essas equações. É de notar que foi adotada esta sequência, pois cada uma delas depende da anterior.

ωi =

π × Di × ni
1000 × 60

(27)

ωi =

π × 90,4551 × 1430
1000 × 60 | ωi =

π × 104,3762 × 357,50
1000 × 60

ωi =

π × 195.8111 × 89.375
1000 × 60 | ωi =

π × 195.8111 × 89.375
1000 × 60

- Fti – força tangencial de engrenamento [N]
- Fri – força radial de engrenamento [N]
- Fai – força axial de engrenamento [N]
- α − ângulo de pressão [º]
- β − ângulo de hélice primitiva do dentado [º]
- Mti – momento torsor a transmitir pelo pinhão [Nm]
- P – potência a transmitir pela engrenagem [W]
- ωi – velocidade angular do pinhão [rad/s]
- Di – diametro primitivo do pinhão [m]
- ni – rotação do pinhão [m]

Mti =

P
ωi

(28)

Mt0 = Tm = 441,45 | Mt1 =

1500
1,9538 = 767,7415

Mt2 =

1500
0,9163 = 1637,0 | Mt3 =

1500
2,3092 = 649,5891

Fti =

Mti
Di/2

(29)

Ft1 =

441,45
90,4551/2
= 9760,6 | Ft2 =

767,7415
104,3762/2

= 14711

Ft3 =

1637
195.8111/2

= 16720

Fri = Fti

tan α
tan β

(30)

Fr1 = 9760,6 ×

tan 20
tan 20 = 3780,6 | Fr2 = 14711 ×

tan 20
tan 35 = 6536,5

Fr3 = 16720 ×

tan 20
tan 40 = 7944,1
Fai = Fti × tan β | (31)
Fa1 = 3780,6 × tan 20 = 3552,6 | Fa2 = 6536,5 × tan 35 = 10301

Fa3 = 7944,1 × tan 40 = 14030

Estas forças serão importantes para calcular as reações presentes nos apoios dos veios e os momentos fletores máximos no local do engrenamento.

Isolando cada veio individualmente, podemos verificar como é que as forças tangenciais e radiais estão distribuídas pelo veio, bem como a dimensão dos mesmos considerando dois planos: OYX e OYZ respetivamente. Os resultados obtidos foram calculados através da ferramenta Ftool e estão apresentados na tabela 10, bem como os diagramas na figura 10 e 11.

Tabela 10 – Forças tangenciais e radiais distribuídas pelos veios.

Veio | Plano | Apoio | R [N]
1 | OYX | a | 100
| | b | 3900
| OYZ | a | -3900
| | b | 5900
2 | OYX | a | 700
| | b | 3400
| OYZ | a | 3900
| | b | 8800
3 | OYX | a | -7100
| | b | -5100
| OYZ | a | -3600
| | b | -1600
4 | OYX | a | -25100
| | b | -33000
| OYZ | a | 3900
| | b | -12900

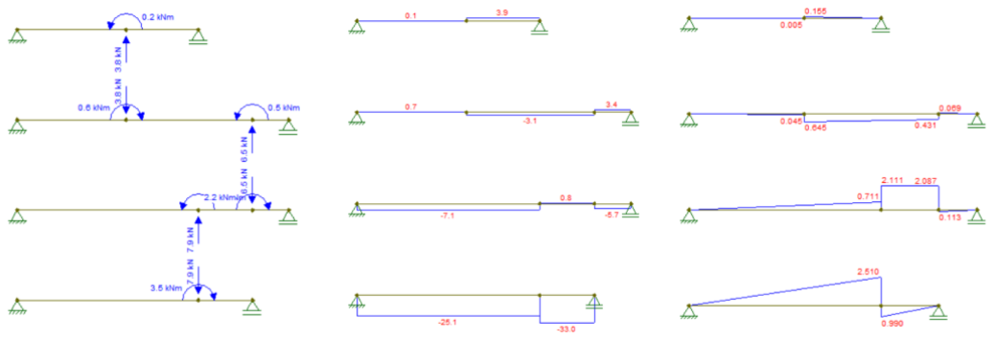
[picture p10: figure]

Figura 10 – Cálculo obtido pela ferramenta Ftool das forças aplicadas no plano OXY, sendo a representação de forças, variação das mesmas e a variação dos momentos respetivamente.

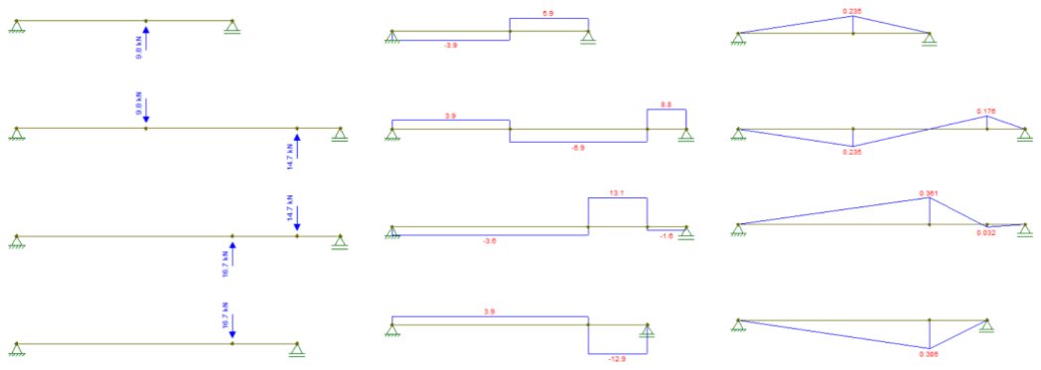
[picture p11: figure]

Figura 11 – Cálculo obtido pela ferramenta Ftool das forças aplicadas no plano OZY, sendo a representação de forças, variação das mesmas e a variação dos momentos respetivamente.

Através destes esquemas e das forças calculadas foi possível determinar as reações nos apoios que estão descritas juntamente com as imagens dos veios.

É de notar que os cálculos das reações foram realizados no software FTool como já foi referido na introdução.

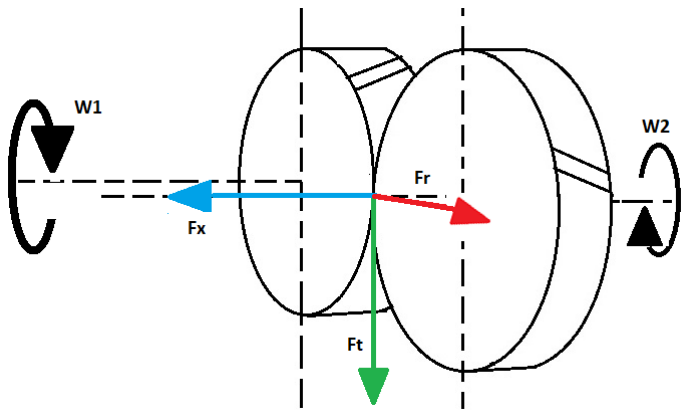
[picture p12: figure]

Figura 12 –Diagrama de forças resultantes entre engrenagens.

3. Dimensionamento de Rolamentos
Para fazer o dimensionamento dos rolamentos, começou-se por calcular as forças de reação nos apoios do veio.

As forças axiais apresentadas nos apoios foram consideradas como sendo a soma das forças axiais de engrenamento.

Estará presente nos apoios forças radiais como forças axiais. Inicialmente optou-se por escolher rolamentos de contacto angular de esferas carreira simples de 25º para o primeiro (a) e segundo (b) apoios. Assim sendo, determinou-se dos fatores de carga. Para isso, recorreu-se às seguintes equações, de onde os resultados estão presentes logo a seguir. É importante salientar que se considerou que os veios irão ter os mesmos rolamentos tanto no lado esquerdo como no lado direito.

3.1. Fatores de carga estáticos
Primeiramente, efetuou-se o cálculo da força radial exercida para cada rolamento dos 4 veios, sendo a correspondente ao primeiro apoio e b ao segundo. Através da equação (32), obteve-se os valores pretendidos.

- Fri – força radial do rolamento [kN]
- Rxy – Reação no plano XY [N]
- Rzy – Reação no plano YZ [N]

Posteriormente, determinou-se os valores dos fatores de carga estáticos, através das equações (32) e (33). Os valores de X0 e Y0 foram retirados da tabela 5.8 [2] para rolamentos de esferas radial-axial, com contacto angular de 40 graus, sendo os seus valores de 0.5 e 0.26 respetivamente.

Para o rolamento do primeiro apoio (a), tem-se:

Para o rolamento do segundo apoio (b), tem-se:

Fri = √(Rxy)
2 + (Rzy)

2
(32)

Fr1,a = √(0,100)
2 + (−3,900)
2 = 3,9013 | Fr1,b = √(3,900)
2 +(5,900)

2 = 7,0725

Fr2,a = √(0,700)
2 + (3,900)
2 = 3,9623 | Fr2,b = √(3,400)
2 +(8,800)

2 = 6,7482

Fr3,a = √(−7,100)
2 + (−3,600)
2 = 7,9605 | Fr3,b = √(−5,100)
2 +(−1,600)

2 = 5,9203

Fr4,a = √(−25,100)
2 + (3,900)
2 = 25,401 | F4,b = √(−33,000) 2 +(−12,900)
2 = 35,432

P0 = X0 × Fr + Y0 × Fa

(
33)

C0 = fs × P0

(
34)
P0,1 = 0,5 × 3,9013
+0,26
× 3,5526
= 2,874

C0,1 = 1,2 × 2,874 = 3,449

P0,2 = 0,5 × 3,9623
+0,26
× 6,7482
= 3,736

C0,2 = 1,2 × 3,736 = 4,486

P0,3 = 0,5 × 7,9605
+0,26
× 3,7288
= 4,950

C0,3 = 1,2 × 4,950 = 5,940

P0,4 = 0,5 × 25,401
+ 0,26
× 14,030
= 16,348

C0,4 = 1,2 × 16,348 = 19,618

P0,1 = 0,5 × 7,0725 + 0,26 × 3,5526 = 4,460 | C0,1 = 1,2 × 4,460 = 5,352
P0,2 = 0,5 × 9,4340 + 0,26 × 6,7482 = 6,472 | C0,2 = 1,2 × 6,472 = 7,776
P0,3 = 0,5 × 5,9203 + 0,26 × 3.7288 = 3,930 | C0,3 = 1,2 × 3,930 = 4,716
P0,4 = 0,5 × 35,432 + 0,26 × 14,030 = 21,364 | C0,4 = 1,2 × 21,364 = 25,636

- C0 – capacidade de carga estática [kN]
- fs – coeficiente de segurança [adimensional]
- P0 – carga estática equivalente [kN]
- X0 – fator radial [adimensional]
- Y0 – fator axial [adimensional]
- Fr – força radial [kN]
- Fa – força axial [kN]
3.2. Fatores de carga dinâmicos
De seguida, calculou-se os fatores de carga dinâmicos, recorrendo às equações 35 e 36. É preciso ter em consideração que na obtenção dos valores de X e Y, for preciso calcular a razão das forças axial e radial, sendo que, para o caso da mesma ser maior que o coeficiente de carga axial (e = 1,14 para rolamentos de esferas radial-axial, com contacto angular de 40 graus), os valores de X e Y são respetivamente 0,35 e 0,57 (caso do veio 2 e 3). Para o caso contrário, os valores tomam-se como 1,0 e 0,0 respetivamente (caso do veio 1 e 4).

Relativamente aos fatores de rotação (retirados da tabela 5.7 [2]), considerou-se os valores de 0,281 para a velocidade do veio 1, 0,405 para a velocidade do veio 2, 0,693 para a velocidade do veio 3 e 0,693 para a velocidade do veio 4. No caso do fator de temperatura considerou-se que a temperatura máxima seria de 120º sendo o seu valor de 1,0. Por fim, o fator dinâmico considerou-se o de motores elétricos pequenos escolhendo-se 1,5.

Para o primeiro apoio (a), tem-se:

Para o segundo apoio (b), tem-se:

- C– capacidade de carga dinâmica [kN]
- P – carga dinâmica equivalente [kN]

P = X × Fr +Y × Fa

(
35)

C =

fl
fn × ft

× P

(
36)
P1 = 1,0 × 3,9013
+ 0,0 × 3,5526
= 3,9013

C1 =

1,5
0,281 × 1

× 3,9013 = 20,825

P2 = 0,35 × 3,9623
+0,57
× 6,7482
= 5,233

C2 =

1,5
0,405 × 1

× 5,233 = 19,383

P3 = 0,35 × 7,9605
+0,57
× 3,7288
= 4,912

C3 =

1,5
0,693 × 1

× 4,912 = 10,631

P4 = 1,0 × 25,401
+ 0,0 × 14,030
= 25,401

C4 =

1,5
0,693 × 1

× 25,401 = 54,981

P1 = 1,0 × 7,0725 + 0,0 × 3,5526 = 7,0725 | C1 =

1,5
| 0,281 × 1

× 7,0725 = 37,753

P2 = 0,35 × 9,4340 + 0,57 × 6,7482 = 7,148 | C2 =

1,5
| 0,405 × 1

× 7,148 = 26,475

P3 = 0,35 × 5,9203 + 0,57 × 3.7288 = 4,198 | C3 =

1,5
0,693 × 1

× 4,198 = 9,086

P4 = 1,0 × 35,432 +0,0 × 14,030 = 35,432 | C4 =

1,5
| 0,693 × 1

× 35,432 = 76,692

- X – fator radial [adimensional]
- Y – fator axial [adimensional]
- Fr – carga radial [kN]
- Fa – carga axial [kN]
- fn – fator de carga de rotação [adimensional]
- fl – fator de esforços dinâmicos [adimensional]
- ft – fator de temperatura [adimensional]

Os resultados obtidos são apresentados na tabela 11, a fim comparar com as características dos fornecedores, arredondados às centésimas.

Tabela 11 – Valores dos fatores de carga estática e dinâmica.

A | Carga Dinâmica | Carga Estática
P [kN] | C [kN] | P0 [kN] | C0 [kN]
Veio 1 | 3,901 | 20,825 | 2,874 | 3,449
Veio 2 | 5,233 | 19,383 | 3,736 | 4,483
Veio 3 | 4,912 | 10,631 | 4,950 | 5,940
Veio 4 | 25,401 | 54,981 | 16,348 | 19,618
B | Carga Dinâmica | | Carga Estática
| P [kN] | C [kN] | P0 [kN] | C0 [kN]
Veio 1 | 7,072 | 37,753 | 4,460 | 5,352
Veio 2 | 7,148 | 26,475 | 6,472 | 7,766
Veio 3 | 4,198 | 9,086 | 3,930 | 4,716
Veio 4 | 35,432 | 76,692 | 21,364 | 25,636

Na tabela 12 encontram-se as características e os números dos rolamentos selecionados no catálogo da RKF.

Tabela 12 - Características dos rolamentos selecionados.

A | Ø Rolamento | Carga Dinâmica | Carga Estática | Designação
| a [mm] | Ca [kN] | C0a [kN]
Veio 1 | 25,0 | 26,5 | 15,3 | 7305 BECBP
Veio 2 | 25,0 | 26,5 | 15,3 | 7305 BECBP
Veio 3 | 17,0 | 11,1 | 6,1 | 7203 BEY
Veio 4 | 45,0 | 55,9 | 37,5 | 7309 BEP
B | Ø Rolamento | Carga Dinâmica | Carga Estática | Designação
| b [mm] | Cb [kN] | C0b [kN]
Veio 1 | 35,00 | 39,00 | 24,50 | 7307 BECBY
Veio 2 | 25,00 | 26,50 | 15,30 | 7305 BECBP
Veio 3 | 25,00 | 26,00 | 15,60 | 7305 BECBP
Veio 4 | 55,0 | 85,0 | 60,0 | 7311 BECBM

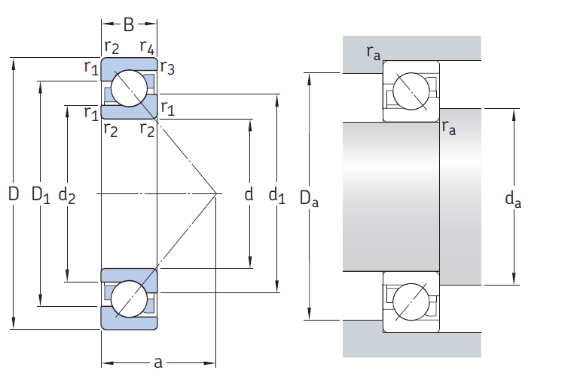
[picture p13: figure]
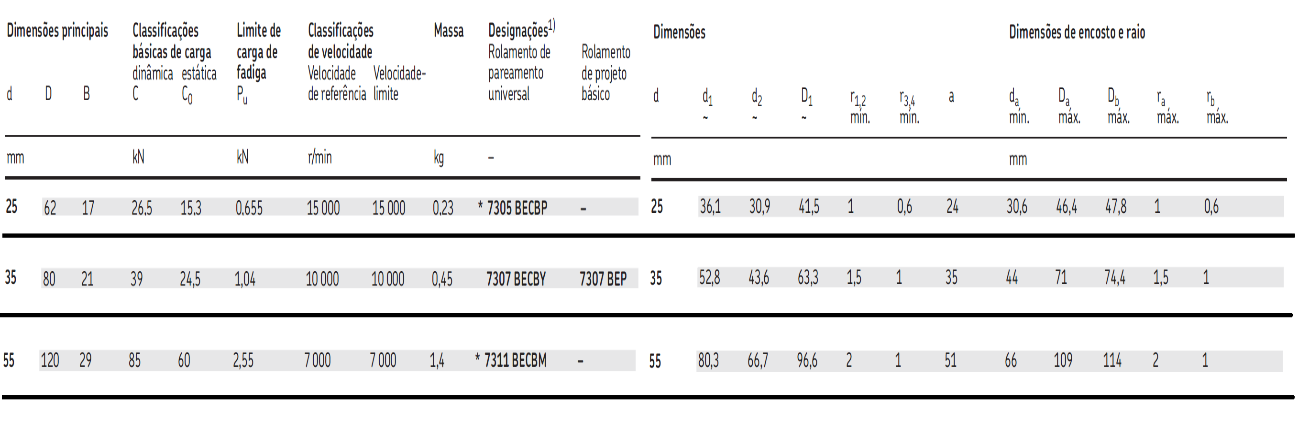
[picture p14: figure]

Figura 13 – Desenho de construção dos rolamentos e suas características dimensionais e mecânicas.

Todos os rolamentos foram selecionados através do catálogo da RKF garantem o diâmetro mínimo compatível com o mecanismo, inclusive, quando montados não irão interferir com a montagem dos outros veios.

4. Dimensionamento do veio
4.1. Critério de Cedência
De modo a garantir a segurança e durabilidade do redutor, em primeiro lugar, realizou-se o dimensionamento do diâmetro mínimo que o veio deverá ter. Para isso recorreu-se aos dois critérios de cedência conhecidos: Tresca e Von Mises, sendo que se escolheu o que garantia um diâmetro mínimo maior entre estes. Para calcular estes dois critérios, teve-se em consideração a tensão normal máxima e a tensão de corte máxima como se verifica nas equações (37) e (38).
- σb,máx − tensão normal máxima [Pa]
- Mb (x) − momento fletor [Nm]
- Di – diâmetro [m]
- τt,máx − tensão de corte máxima [Pa]
- Mt (x) − momento torsor [Nm]
- Di – diâmetro [m]

Como se pode observar, estas equações dependem tanto do momento torsor como do momento fletor. O momento torsor pode ser calculado através da equação 37 e da qual se obteve os resultados para cada veio.

(σb,máx)i =

32 × Mb(x)
π × Di

3

(37)

(τb,máx)i =

16 × Mt(x)
π × Di

3

(38)

Já o momento fletor foi calculado através do software FTool, nos planos OXY e OXZ.

4.1.1. Critério de Tresca
Tendo os valores para cada plano, procedeu-se então primeiro ao cálculo do critério de Tresca. Este pode ser visto na equação (39) obtida através das expressões 36 e 37, bem como o seu resultado. Assim, rearranjou-se a equação (40) para se determinar esse diâmetro mínimo. Para os veios 1 e 2, a tensão de cedência é 430 MPa, correspondendo ao aço Ck45 tempera mais revenido; para os veios 3 e 4, ela é 750 MPa, correspondendo ao aço 42CrMo4 tempera mais revenido.
- Mb(x) – momento fletor [Nm]
- Mt(x) – momento torsor [Nm]
- Di – diâmetro mínimo [m]
- σy – tensão de cedência do material [Pa]
- y fator de segurança [adimensional]
4.1.2. Critério de Von Mises
Mais tarde, recorreu-se ao critério de Von Mises usando as equações (41) e (42), obtendo-se os resultados indicados a seguir. Os valores para a tensão de cedência são os mesmos utilizados para o critério anterior.

σy
y

≥ √(σb,máx)
2 + 4 × (τb,máx)

2
<=>

σy
2 × y

≥ √(
16 × Mb

(x)
π × Di

3

)

2
+ (
16 × Mt

(x)
π × Di

3

)

2
(39)

Di ≥ √
32 × y
π × σy

× √Mb(x)
2 + Mt(x)

2

3
(40)

D1 ≥ √
32 × 1,5
π × 430 × 10⁶

× √281,5138² + 441,4500²

3
≥ 0,0265

D2 ≥ √
32 × 1,5
π × σy

× √686,4765² + 767,7415²

3
≥ 0,0332

D3 ≥ √
32 × 1,5
π × 750 × 10⁶

× √2141,645² + 1636,9646²

3
≥ 0,0380

D4 ≥ √
32 × 1,5
π × 750 × 10⁶

× √2539,507² + 649,5891²

3
≥ 0,0377

- Mb(x) – momento fletor [Nm]
- Mt(x) – momento torsor [Nm]
- Di – diâmetro mínimo [m]
- σy – tensão de cedência do material [Pa]
- y - fator de segurança [adimensional]

Fazendo agora uma comparação com os valores tanto do critério de Tresca como o de Von Mises, e tendo em consideração as séries de Renard como critério de normalização, chegou-se a conclusão de que os diâmetros mínimos dos veios serão os seguintes:

- Dveio,1= 35 mm;
- Dveio,2= 25 mm;
- Dveio,3= 25 mm;
- Dveio,4= 55 mm.

É importante salientar que estes diâmetros já dispõem de correções eventuais futuras. Sendo que os diâmetros que foram escolhidos inicialmente não passavam nos critérios de fadiga.

4.2. Critério de Rigidez
Para avaliar a rigidez do veio, tem-se em consideração o diâmetro mínimo e o material utilizado. Para determinar se o veio é rígido o suficiente, mediu-se a flecha nos pontos de engrenamento e a rotação nos apoios para o plano OZY. Nesta medição recorreu-se ao software FTool. Nas imagens seguintes é possível visualizar os resultados das flechas e rotações.

Tabela 13 – Flexas e rotações dos veios .

Veio | Rotação / Flexa | Valor | Limite
Veio 1 | Rot. esquerda | 1,797e-3 rad | 3e-3 rad
| Flexa Z1 | 1,314e-2 mm | 2.5 mm
| Rot. direita | 4,257e-4 rad | 3e-3 rad
Veio 2 | Rot. esquerda | 1,797e-3 rad | 3e-3 rad
| Flexa Z2 | 7,104e-2 mm | 2,5 mm
| Flexa Z3 | -5,452e-3 mm | 2,25 mm

σy
y

≥ √(σb,máx)
2 + 3 × (τb,máx)
<=>

σy
2 × y

≥ √(
16 × Mb

(x)
π × Di

3

)

+ (
16 × Mt

(x)
π × Di

3

)
(41)

Di ≥ √
32 × y
π × σy

× √Mb(x)
2 + 0,75 × Mt(x)

2

3
(42)

D1 ≥ √
32 × 1,5
π × 430 × 10⁶

× √281,5138² + 0,75 × 441,4500²

3
≥ 0,0256

D2 ≥ √
32 × 1,5
π × σy

× √686,4765² + 0,75 × 767,7415²

3
≥ 0,0324

D3 ≥ √
32 × 1,5
π × 750 × 10⁶

× √2141,645² + 0,75 × 1636,9646²

3
≥ 0,0374

D4 ≥ √
32 × 1,5
π × 750 × 10⁶

× √2539,507² + 0,75 × 649,5891²

3
≥ 0,0376

| Rot. direita | 1,193e-4 rad | 3e-3 rad
Veio 3 | Rot. esquerda | 2,960e-3 rad | 3e-3 rad
| Flexa Z4 | 1,391e-1 mm | 2.25 mm
| Flexa Z5 | 5,961e-2 mm | 3 mm
| Rot. direita | 2,952e-3 rad | 3e-3 rad
Veio 4 | Rot. esquerda | -1,145e-04 rad | 3e-3 rad
| Flexa Z6 | -4,295e-3 mm | 3 mm
| Rot. direita | -1,646e-04 rad | 3e-3 rad

Como podemos ver, todos os veios passam no critério de rigidez sendo que não é preciso sofrerem alterações de correção.

5. Dimensionamento de chavetas / veios estriados
De modo a conseguir transmitir o momento torsor da engrenagem para os veios, é necessário dimensionar chavetas ou veios estriados.

No caso deste projeto, o dimensionamento foi feito na totalidade para chavetas.

O dimensionamento de chavetas relaciona-se com a resistência ao corte do material da chaveta (τa adm) e também com a resistência à compressão-esmagamento desse material (σd adm).

Assim para começar a fazer o dimensionamento definiu-se a tensão de corte admissível como 85 MPa, pois esta varia entre 70 e 100 MPa, sendo o valor máximo entre estes para situações em que a solicitação seja constante. Já para a tensão de esmagamento admissível foi selecionado, através da tabela 6.2 do livro [2], o valor de 80 MPa.

De seguida, tendo em consideração o diâmetro de cada veio e após a consulta da tabela 6.1 do livro [2] com as dimensões das chavetas paralelas, podemos determinar as dimensões das chavetas para cada diâmetro de cada veio.

Depois, através das equações 43 e 44, ver se as condições de resistência ao corte e ao esmagamento se verificaram e assim determinar o comprimento mínimo da chaveta (L).

(43)

(44)

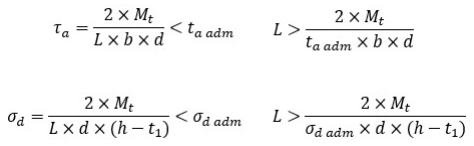
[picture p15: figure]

O comprimento do cubo (lc) deve ser 10 mm mais longo do que o comprimento da chaveta e também deve ser menor do que 2,5 vezes o diâmetro, se for superior é melhor escolher uma secção estriada. Como todas as rodas dentadas corresponderam a este critério, não houve problema e dimensionou-se apenas chavetas.

As características das chavetas podem ser consultadas na tabela abaixo.

Tabela 14 – Chavetas dimensionadas.

Veio | Roda dentada | L [mm] | b [mm] | h [mm] | t1 [mm] | t2 [mm]
1 | Z1 | 25 | 10 | 8 | 5 | 3,3
2 | Z2 | 25 | 8 | 7 | 4 | 3,3
2 | Z3 | 45 | 8 | 7 | 4 | 3,3
3 | Z4 | 45 | 8 | 7 | 4 | 3,3
3 | Z5 | 25 | 8 | 7 | 4 | 3,3
4 | Z6 | 25 | 16 | 10 | 6 | 4,3

4.3. Esboços dos veios
Recorrendo a todos os dimensionamentos foi possível desenhar os primeiros esboços dos veios a usar no redutor. Para isso, recorreu-se ao software SolidWorks sendo possível observar os resultados obtidas nas figuras apresentadas a seguir.

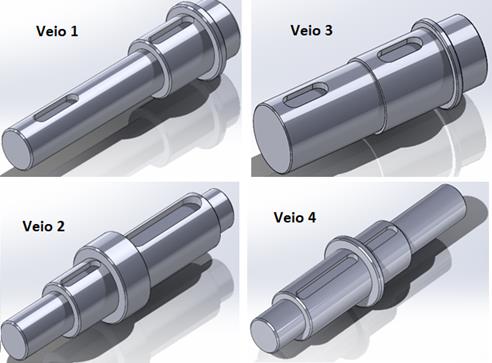
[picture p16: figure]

Figura 14 – Modelação dos veios

7.2 Definição do acoplamento
Após o dimensionamento e seleção dos rolamentos e veios podemos escolher o acoplamento mais indicado para esta aplicação. Optou-se por um Rotex acoplamento elástico modelo S-H, estes são de fácil montagem/desmontagem radial, a substituição do elastômero não necessita deslocação dos eixos a nível axial, é livre de manutenção e fácil inspeção visual, compacto e possuí ótimas propriedades dinâmicas, com baixo efeito rotacional e alto torque graças à sua geometria.

Binário Nominal

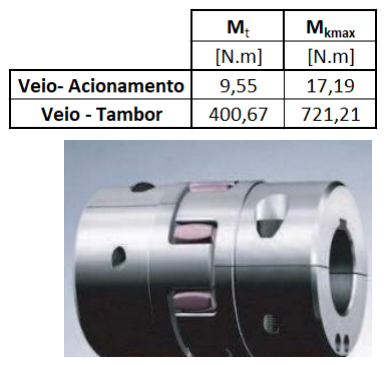
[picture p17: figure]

Binário Máximo

Figura 15 – Desenho construção acoplamento tipo S-H.

6. Conclusão

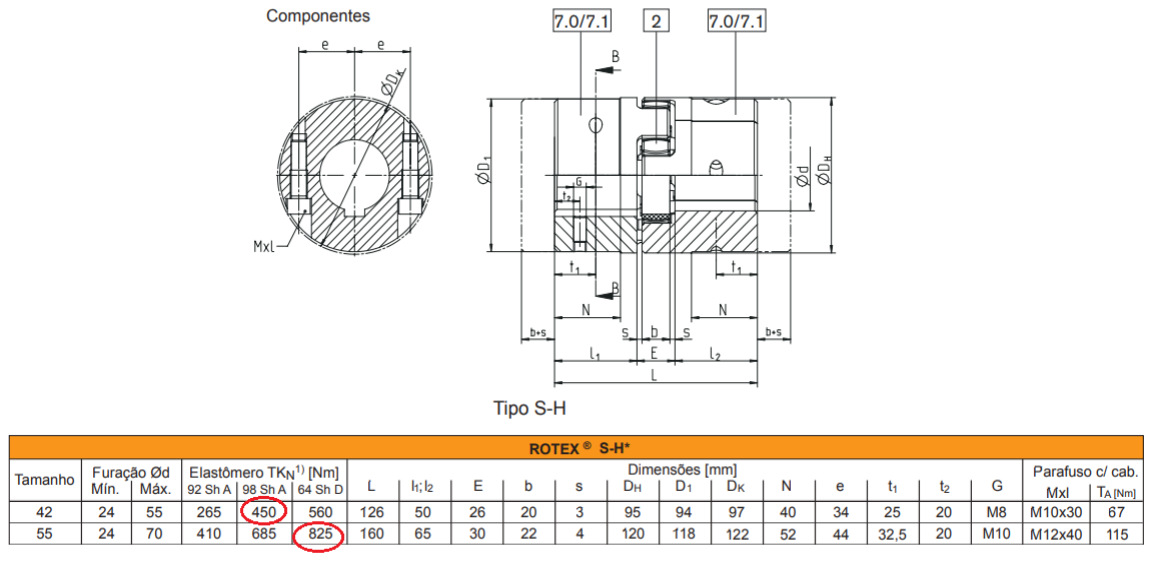
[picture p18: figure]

Neste relatório começamos por otimizar parâmetros e valores calculados no relatório anterior, tais como, seleção do cabo de aço, dimensionamento do tambor, posição da roldana de apoio e otimização das engrenagens.
O cabo de aço previamente selecionado era substancialmente sobredimensionado, numa forma de otimização optamos por um cabo de diâmetro menor e do tipo 6x7 CF que também é para o mesmo tipo de funções e com o mesmo fator de segurança. Esta alteração leva-nos a redimensionar o tambor, que terá de ter a capacidade pelo menos 23 voltas com uma elevação de ranhura de 0,005 m e comprimento mínimo de 0,12 m. A roldana de apoio (guia) deverá ser colocada a 1,9 m de distância do tambor, em que o ângulo ß será de 2º. Ao nível das engrenagens, foi possível alterar os cálculos de modo a reduzir a qualidade do material e consequentemente reduzir o seu custo. Isto resultou da alteração dos dentes e consequentemente o dos módulos também. No entanto, temos a plena noção de que os valores ainda podem ser mais otimizados com a escolha de um motor com um numero mais reduzido de rotação.
Nesta segunda fase após efetuarmos as melhorias necessárias demos seguimento ao projeto, tal como o dimensionamento dos veios e chavetas, selecionamento de rolamentos e dos acoplamentos.
Para um dimensionamento dos veios começamos por um processo de identificação das forças resultantes de engrenamento, desde a força radial, tangencial e axial. Conseguimos obter os valores as reações normais para cada veio e para cada seu ponto de apoio (Tabela
10) e a representação do momento fletor em cada um dos mesmos (Figura 10 e 11).
Após conclusão do passo anterior tínhamos os dados suficientes para calcular a carga estática e dinâmica em cada um dos apoios e depois podermos selecionar os rolamentos mais adequados para cada uma das situações (Tabela 12). Optamos por rolamentos de contacto angular de esferas de carreira simples (Tabela 13).
No encadeamento do processo, após identificação das forças, cálculos das cargas, seleção de rolamentos, já podemos dimensionar os veios. Aplicamos dois métodos de cedência, Tresca (conservador) e o Von Mises (vanguardista) conseguimos obter um diâmetro mínimo.
Conjugando todos estes fatores podemos por fim selecionar o acoplamento mais indicado para esta aplicação, optamos por um acoplamento do tipo S-H, visto que é de fácil aplicação, não necessita manutenção e entre outras boas vantagens.

O grupo tem a noção que o dimensionamento dos veios há fadiga está em falta, no entanto, este já foi iniciado. Como se encontra numa fase bastante inicial foi optando por não se colocar aqui. Este atraso deveu-se há enorme perda de tempo a tentar corrigir os problemas do primeiro relatório. Os cálculos há fadiga serão devidamente apresentados no próximo momento de avaliação.

Referências

[1] GGR Group. “Easy Big WH-KI Ladder Hoist”. Consultado a 11 de março de 2023, em https://www.ggrgroup.com/products/ladder-hoists/easy-big-wh-ki-ladder-hoist/
[2] Completo, A., Melo, F. Q. (2019). Introdução ao Projeto Mecânico, Segunda Edição, Engebook.
[3] Rasmussen Equipment Co. “6×25 Filler Wire With IWRC”. Consultado a 25 de fevereiro, em https://www.raseq.com/wire-rope/6x25-filler-wire-with-iwrc/
[4] Randers Reb. “Handling, Inspection and Installation”. Consultado a 1 de março de 2023, em https://www.randers-reb.com/fishing-rope/rope-technology/handling-inspection-and-installation (https://www.randers-reb.com/fishing-rope/rope-technology/handling-inspection-and-installation)
[5] Eletrolift. “Drums”. Consultado a 2 de março de 2023, em https://electrolift.com/product/drums/
[6] Remain. "Motores Elétricos Trifásicos IEC com freio DC - Série BCL”. Consultado a 5 de março de 2023, em https://reiman.pt/pt/bcl-three-phase-motor-with-dc-brake/
[7] WEG S. A. “Motores Trifásicos”. Consultado a 18 de fevereiro de 2023, em https://www.weg.net/institutional/PT/pt/
[9] KTR Catálogo de Acoplamentos ROTEX

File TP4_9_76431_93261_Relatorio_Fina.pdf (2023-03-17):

# 2021/2022 Relatório final: Dimensionamento

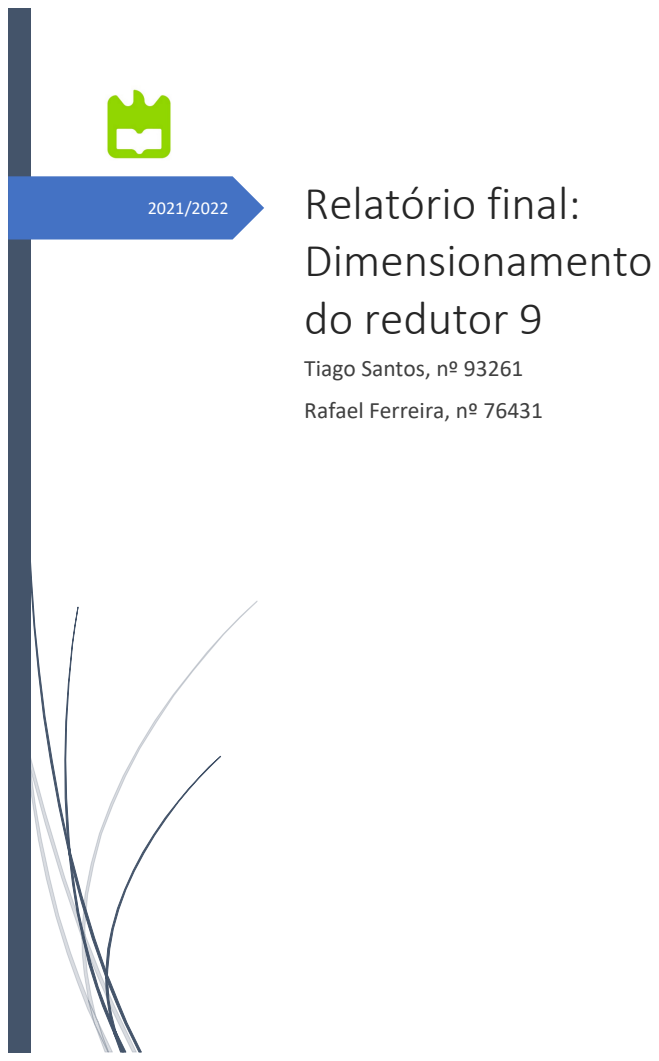
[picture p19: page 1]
do redutor 9

Tiago Santos, nº 93261
Rafael Ferreira, nº 76431

## Índice

## PARTE 1

### Introdução

Um redutor de velocidades é um dispositivo mecânico que permite, como o nome indica reduzir a velocidade de um acionador (neste caso, de um motor), mantendo a potência constante. Este tipo de dispositivo é bastante usado na indústria para transmitir a potência do motor reduzindo a velocidade e aumentando o binário, permitindo assim, por exemplo, o transporte de grandes cargas como num elevador.

Neste relatório, vai ser abordado o procedimento do dimensionamento das engrenagens de um redutor de velocidades de eixos paralelos com veio de entrada e saída coaxiais, sendo que o sistema de engrenamento deve ser composto por rodas dentadas helicoidais. É importante referir que o motor que irá acionar este redutor possui uma potência de 22 kW produzindo uma rotação com velocidade de 1500 rpm. À saída do redutor, o veio deverá ter uma velocidade de 80 rpm. O exterior do redutor deverá ser formado por um cárter de alumínio fundido permitindo um fácil acesso interno de modo a facilitar a manutenção do redutor.

O redutor dimensionado neste projeto terá 3 níveis de engrenagens com uma relação de 3:1; 2,5:1 e 2,5:1 sendo que o módulo destas foi dimensionado de acordo com dois métodos: a rutura de em flexão do dente e a fadiga por ação de tensões de contacto durante o engrenamento, mais conhecido por tensões de Hertz. Após os cálculos, foram comparados os módulos obtidos para cada engrenagem escolhendo-se o módulo obtido pelo critério que apresentava uma maior segurança. Já com o valor dos módulos calculados, obteve-se o resto dos valores importantes para as engrenagens e, por fim, corrigiu-se o dentado para eliminar a interferência de corte e para a eliminação da variação do entre eixo. Estes cálculos serão mais bem explicados nas secções seguintes.

### Dimensionamento das engrenagens

Como referido na introdução, começou-se por determinar o número de andares que o redutor irá ter. Para isso recorreu-se à equação 1 obtendo-se um valor de 2,11, ou seja, 3 andares.

Nandares =

log10(

ωentrada
ωsaída

)

log10(4)

(1)

Nandares =

log10 (

1500
80 )

log10(4)

≈ 2,11 = 3

- Nandares − número de andares [adimensional]
- ωentrada − velocidade de entrada [rpm]
- ωsaída − velocidade de saída [rpm]

Depois, desenhou-se um esboço do esquema cinemático de modo a ter uma visualização de como se iria organizar o interior do redutor a ser dimensionado. Este esquema é meramente ilustrativo e demonstra como se pensou durante a distribuição das engrenagens ao longo dos níveis. O esboço pode ser visto na figura 1.

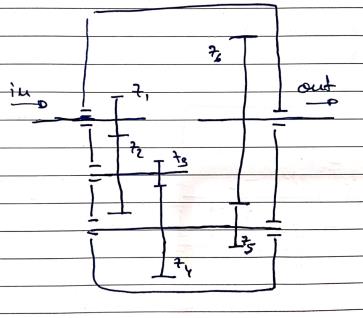
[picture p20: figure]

Figura 1 – Esboço do esquema cinemático.

De seguida, obteve-se a relação de transmissão total através da equação 2, sendo que, esta será em função da razão entre a velocidade de entrada e velocidade de saída. Foi obtido um valor de 18,75 de onde resultou, posteriormente, o valor da relação de transmissão de cada engrenagem através da equação 3, obtendo-se então as relações de 3:1; 2,5:1 e 2,5:1 retratando respetivamente os andares 1, 2 e 3. Para cada saída de nível obteve-se uma velocidade de 600 rpm, 200 rpm e 80 rpm respetivamente.

UTotal =

ωentrada

ωsaida

(2)

UTotal =

ωentrada

ωsaida

=

1500
80 = 18,75

- UTotal − Relação de transmissão total [adimensional]
- ωentrada − velocidade de entrada [rpm]
- ωsaída − velocidade de saída [rpm]

UTotal = u1

. u2

. u3
(3)

UTotal = u1

. u2

. u3 = 3 ∗ 2,5 ∗ 2,5 = 18,75

- UTotal − Relação de transmissão total [adimensional]
- u1 − relação de transmissão do primeiro andar [adimensional]
- u2 − relação de transmissão do segundo andar [adimensional]
- u3 − relação de transmissão do terceiro andar [adimensional]

Através das relações de transmissão de cada andar e arbitrando o número de dentes (Z) inicial para o pinhão, obteve-se o número de dentes da roda através da relação apresentada pela equação 4. Os valores obtidos foram sendo alterados com o decorrer dos cálculos de modo a determinar um melhor módulo e tornando o redutor o mais compacto possível. O valor do número de dentes pode ser visualizado na tabela 1.

u =

Zroda

Zpinℎão

≡ Zroda = u. Zpinℎão
(4)

Zroda 1 = u1

. Zpinℎão 1 = 3 ∗ 12 = 36

Zroda 2 = u2

. Zpinℎão 2 = 2,5 ∗ 16 = 40

Zroda 3 = u3

. Zpinℎão 3 = 2,5 ∗ 30 = 75

- u − relação de transmissão [adimensional]
- Zpinhão − número de dentes do pinhão [adimensional]
- Zroda − número de dentes da roda [adimensional]

Tabela 1 – Número de dentes das engrenagens.

Nível da engrenagem | Pinhão | Roda
1 | 12 | 36
2 | 16 | 40
3 | 30 | 75

Como podemos ver, o número de dentes do pinhão do nível 1 e 2 são inferiores ao número de dentes mínimo de um pinhão talhado por cremalheira ou fresa-mãe (1) sendo que, mais à frente, durante a determinação dos diâmetros, será necessário calcular um incremento de correção de modo a eliminar a interferência de corte.

Após a obtenção dos dentes de cada roda dentada procedeu-se então ao cálculo do módulo da engrenagem. Este módulo foi dimensionado utilizando dois métodos: a rutura de em flexão do dente e a fadiga por ação de tensões de contacto durante o engrenamento, mais conhecido por tensões de Hertz, sendo que será escolhido o maior módulo obtido entre estes dois métodos. Este irá corresponder aos critérios de segurança impostos por cada método.

De modo a conseguir calcular o módulo, foi necessário o cálculo dos parâmetros presentes nas equações de cada um dos métodos. A maneira como foram efetuados esses cálculos pode ser visualizada na tabela 2 bem como os resultados obtidos e informações necessárias para a compreensão dos valores obtidos. É de salientar que foi utlizado um aço de liga crômio-molibdênio (42CrMo4) uma vez que é um aço bastante utilizado na produção de engrenagens. O uso deste material justifica os valores assumidos para o módulo de elasticidade
(E) e para o coeficiente de Poisson, uma vez que são correspondentes a esta liga de aço.

Tabela 2 – Parâmetros necessários ao cálculo dos módulos.

Parâmetro | Símbolo | Expressão | Resultado | Observação
Fator proporcional largura/módulo | CLβ | (CL = L/mn) CLβ = CL/cosβ | (12) 12,77 | 1*
Fator de efeito do dentado helicoidal | Yβ | Yβ = 1/cosβ | 1,06 | β = 20º
Fator de efeito dinâmico | KM | - | 1 | 2*
Fator de duração | KbL | KbL = log10(NLh)/8 | 1,20 | 3*
Fator de fadiga à tensão de contacto | KHL | KHL = 8/log10(NLh) | 0,83 | 3*
Fator de alinhamento | KA | KA = 1 se L/d1<1 | 1 | L/d1 é < 1
Fator de condução | Yε | - | 0,8 | admitido
Fator de concentração de tensões | YF | YF = 0,4 se x = 0 | 0,4 | Correção do dentado (x) é igual a 0. 4*
Módulo de elasticidade | E | - | 210 GPa | Módulo para liga utilizada
Coeficiente de Poisson | v | - | 0,3 | Coeficiente para a liga utilizada
Rotação do pinhão | n1 | - | 1500 rpm | Dados do projeto

1* - Valor de CL retirado da tabela 4.7 do (1), porque potência é maior que 10 kW e são rodas helicoidais, optou-se pelo valor de 12.

2* - Valor de KM retirado da tabela 4.5 do (1), optando-se pela entrada (máquina motriz) e saída (máquina acionada) em movimento uniforme.

3* - NLh (Número de ciclos do pinhão) = 20 anos * 300 dias * 8 horas * 60 minutos * 1500 rpm

4*- Valores assumidos inicialmente. Após o cálculo do módulo realizou-se a correção do dentado alterando posteriormente este valor. No entanto, a substituição não alterou os módulos significativamente.

Após o cálculo das incógnitas necessárias, recorreu-se às equações 5 e 6 para calcular o módulo à rotura de fadiga em flexão do dente e à fadiga por ações de tensões de contacto (tensões de Hertz), respetivamente. Obteve-se os valores presentes na tabela 3.

mn ≥ √
1,96×10⁴×P×cosβ×KM×KbL×Yε

CLβ×σbLimite×n1×KA×ZV1×YF×Yβ

× (

u+1
u

)
3
(5)

mn1 ≥ √
1,96×10⁴×22×10³×cos(20)×1×1,20×1

12,77×295×1500×1×14,46×0,4×1,06

× (

3+1
3

)

3
= 2,65

mn2 ≥ √
1,96×10⁴×22×10³×cos(20)×1×1,20×1

12,77×295×500×1×19,28×0,4×1,06

× (

2,5+1
2,5

)

3
= 3,54

mn3 ≥ √
1,96×10⁴×22×10³×cos(20)×1×1,20×0,8

12,77×295×200×1×36,15×0,4×1,06

× (

2,5+1
2,5

)

3
= 3,61
- mn − módulo real da engrenagem [mm]
- P − potência a transmitir pela engrenagem [W]
- σbLimite − tensão limite de fadiga à flexão [MPa]
- u − razão de transmissão [adimensional]
- CLβ − fator proporção largura / módulo [adimensional]
- n1 − rotação pinℎão [rpm]
- ZV1 − número de dentes virtual do pinℎão [adimensional]
- KM − fator de efeito dinâmico [adimensional]
- KA − fator de alinℎamento [adimensional]
- KbL − fator de fadiga por flexão[adimensional]
- Yε − fator de condução [adimensional]
- YF − fator de concentração de tensões à flexão [adimensional]
- Yβ − fator de efeito do dentado ℎelicoidal [adimensional]
- β − ângulo de ℎélice primitiva do dentado [°]
- "+" − utilizar em engrenagens externas

mn ≥ √
6×10⁴×P×cosβ×KM

π²×CLβ×σHLim2×n1×KA×ZV1

2×KHL×sin(2α)

×

2×E
(1−v

2)

× (

u+1
u

)
3
(6)

mn1 ≥ √
6×10⁴×22000×cos(20)×1
π²×12×965²×1500×1×12²×0,83×sin(2×20)

×

2×210000
(1−0,3

2)

× (

3+1
3

)

3
= 4,00

mn2 ≥ √
6×10⁴×22000×cos(20)×1
π²×12×965²×500×1×16²×0,83×sin(2×20)

×

2×210000
(1−0,3

2)

× (

2,5+1
2,5

)

3
= 4,84

mn3 ≥ √
6×10⁴×22000×cos(20)×1
π²×12×965²×200×1×30²×0,83×sin(2×20)

×

2×210000
(1−0,3

2)

× (

2,5+1
2,5

)

3
= 4,32
- mn − módulo real da engrenagem [mm]
- P − potência a transmitir pela engrenagem [W]
- σHLim − tensão limite de fadiga de contacto [MPa]
- u − razão de transmissão [adimensional]
- CLβ − fator proporção largura / módulo [adimensional]
- n1 − rotação pinℎão [rpm]
- ZV1 − número de dentes virtual do pinℎão [adimensional]
- KM − fator de efeito dinâmico [adimensional]
- KA − fator de alinℎamento [adimensional]
- KHL − fator de fadiga à tensão de contacto [adimensional]
- α − ângulo de pressão [°]
- β − ângulo de ℎélice primitiva do dentado [°]
- E − módulo de elasticidade [MPa]
- ν − coficiente de poisson [adimensional]
- "+" − utilizar em engrenagens externas

Tabela 3 – Módulos da fadiga em flexão e da fadiga em contacto obtidos.

| Módulos da fadiga em flexão [mm] | Módulo normalizado [mm] | Módulos da fadiga em contacto [mm] | Módulo normalizado [mm] | Módulo final [mm]
u1 | 2,65 | 2,75 | 4,00 | 4,00 | 4,00
u2 | 3,54 | 3,75 | 4,84 | 5,00 | 5,00
u3 | 3,61 | 3,75 | 4,32 | 4,50 | 4,50

Já com os valores do módulo das engrenagens definidos, procedeu-se ao cálculo dos parâmetros finais das engrenagens. Na tabela 4 pode-se consultar como se obteve o resultado para cada parâmetro. Os resultados obtidos podem ser consultados na tabela 5.

Tabela 4 – Tabela retirada de (1), com os parâmetros geométricos associados ao dentado helicoidal.

Parâmetro | Símbolo | Expressão | Unidades
Módulo aparente | mt | mt = mn / cosβ | mm
Passo | p | p = mn · π | mm
Passo aparente | pt | pt = mt · π | mm
Ângulo de pressão nominal | α | α = 20° | °
Ângulo de pressão aparente | αt | tanαt = tanα / cosβ | °
Diâmetro primitivo | D | D = Z · mt | mm
Diâmetro de base | Db | Db = D · cos αt | mm
Ângulo de dentado | β | β = [0°,5°,10°,15°,20°,25°,30°,35°,40°,45°] | °
Número de dentes | Z | Atribuído | adimensional
Número de dentes virtual | Zv | Zv = Z / cos³β | adimensional
Largura da roda | L | a ser dimensionado ou adotado | mm
Largura do dentado | Lt | Lt = L / cos β | mm
Diâmetro do pé de dente | Dp | Dp = D – 2 · hf | mm
Diâmetro externo (cabeça) | De | De = D + 2 · mn | mm
Altura total do dente | hz | hz = 2,25 · mn | mm
Altura da cabeça do dente | hc | hc = mn | mm
Altura do pé do dente | hf | hf = 1,25 · mn | mm
Folga da cabeça | s | s = 0,25 · mn | mm
Razão de transmissão | u | u = Z2 / Z1 = D2 / D1 = n1 / n2 | adimensional
Entre eixo | e | e = [(Z2 + Z1) / 2] · mt | mm

Tabela 5 – Resultados obtidos para os parâmetros geométricos associados ao dentado helicoidal.

| Resultado
Parâmetro | u1 | u2 | u3
mt | 4,26 | 5,32 | 4,79
p | 12,57 | 15,71 | 14,14
pt | 13,37 | 16,72 | 15,04
α | 20,00 | 20,00 | 20,00
αt | 21,17 | 21,17 | 21,17
D | 48/144 | 80/200 | 135/338*
Db* | 44,76/134,28 | 74,60/186,50 | 125,89/314,72
β | 20,00 | 20,00 | 20,00
Z (pinhão / roda) | 12/36 | 16//40 | 30/75
Zv | 14,46 | 19,28 | 36,15
L | 48,00 | 60,00 | 54,00
Lt | 51,08 | 63,85 | 57,47
Dp* | 38/134 | 67,5/187,5 | 123,75/326,25
De* | 56/152 | 90/210 | 144/346,50

hz | 9,00 | 11,25 | 10,13
hc | 4,00 | 5,00 | 4,50
hf | 5,00 | 6,25 | 5,63
s | 1,00 | 1,25 | 1,13
u | 3,00 | 2,50 | 2,50
e | 102,16 | 148,98 | 251,41

*É importante salientar que estes valores são iniciais ainda sem a correção de entre eixo ou do dentado aplicada. Esta será devidamente mencionada e explicada mais a frente.

Com os parâmetros todos calculados, desenhou-se o primeiro esquema cinemático do redutor de modo a avaliar se as engrenagens não intercetam veios ou se há erros na arquitetura do mesmo. De modo a ter uma perceção da coaxialidade dos veios de entrada e de saída, utilizou-se para os diâmetros das rodas dentadas, os valores do diâmetro primitivo (D) calculados anteriormente e presentes na tabela 5. O resultado do esquema cinemático inicial pode ser dado através da figura 2. É de referir que o esquema já se encontra à escala e, apesar de não se reparar, não existe coaxialidade entre o eixo de entrada e o eixo de saída.

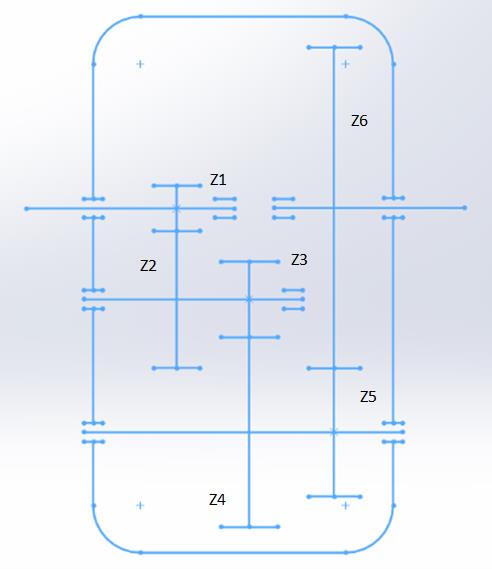
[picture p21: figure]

Figura 2 – Esquema cinemático inicial.

Nos cálculos apresentados anteriormente existem valores a ser corrigidos. O número de dentes escolhido para o pinhão do primeiro e segundo nível são inferiores ao número de dentes mínimo de um pinhão talhado por cremalheira ou fresa-mãe (Z’>17) (1). Por essa razão, tem de se fazer uma correção ao tamanho do dente de modo a eliminar a interferência de corte nas engrenagens dos níveis 1 e 2.

Para determinar os valores mínimos de correção (X1 e X2) utilizaram-se as expressões dadas pelas equações 7 e 8 em função do número de dentes atribuído e do número de dentes mínimo.

X1 =

(Z

´− Z1)

Z

´

(mm) (7)

X11 =

(17 − 12)
17 = 0,29 mm

X12 =

(17 − 16)
17 = 0,059 mm

X2 = −X1
(mm) | (8)

X21 = −0,29 mm

X22 = −0,059 mm

- X1 e X2 − valores mínimos de correção sem variação de entre eixo [mm]

Obteve-se os valores de X1 = 0,29 e X2 = −0,29 para a engrenagem do primeiro nível e os valores de X1 = 0,059 e X2 = −0,059 para a engrenagem do segundo nível. Após a obtenção dos valores de correção, calculou-se os valores do diâmetro exterior para cada uma das rodas dentadas utilizando as fórmulas apresentadas nas equações 9 e 10.

Depinℎão

= D + 2 ∗ (m + X1 ∗ m) (mm) | (9)

Depinℎão1

= 48 + 8 = 56 mm

Depinℎão2

= 80 + 10 = 90 mm

Depinℎão3

= 135 + 9 = 144 mm

- Depinhão − Diâmetro exterior do pinhão [mm]
Deroda = D + 2 ∗ (m + X2 ∗ m) | (mm) | (10)

Deroda1

= 144 + 8 = 152 mm

Deroda2

= 200 + 10 = 210 mm

Deroda3

= 337,5 + 9 = 346,5 mm

- Deroda − Diâmetro exterior da roda [mm]

É preciso também corrigir a falta de coaxialidade do redutor. Para isso, usou-se a correção do dentado com variação de entre eixo. Inicialmente determinaram-se os entre eixos das engrenagens, utilizando as equações 11, 12, 13 e 14, sendo que o entre eixo a ser igualado (veio de entrada) será a soma dos entre eixos dos níveis 1 e 2. O entre eixo do nível 3 (veio de saída) encontra-se superior em 0,25 mm ao entre eixo a ser igualado.

a1

´ =

Zpinℎão1+Zroda1
2
× m (mm) | (11)

a1

´ =

12 + 36
2

× 4 = 96 mm

a2

´ =

Zpinℎão3+Zroda2
2
× m (mm) | (12)

a1

´ =

16 + 40
2

× 5 = 140 mm

a

´ = a1

´ + a2

´ | (mm) | (13)

a

´ = 96 + 140 = 236 mm

- a

´ − entre eixo de funcionamento [mm]
- m − módulo normalizado [mm]
- Zpinhão − número de dentes do pinhão [adimensional]
- Zroda − número de dentes da roda [adimensional]

a =

Zpinℎão3+Zroda3
2
× m (mm) | (14)

a =

30 + 75
2

× 4,5 = 236,25 mm

- a − entre eixo normal [mm]

O passo seguinte foi determinar o novo ângulo de funcionamento da engrenagem, dado pela equação 15, sendo que se obteve um valor de α

′ = 19,83° . Com este ângulo foi possível determinar o somatório da correção (X1 + X2
) pela equação 16, determinando, finalmente e após a verificação da folga de engrenamento nula com a equação 17, as correções individuais através das equações 18 e 19, cujo resultado foi de X1 = 0,198 e X2 = −0,254.

No cálculo feito a partir da equação 18 considerámos λ = 0,5 , sendo que para engrenagens redutoras 0,5 ≤ λ ≤ 0,75.

cosα´ ∗ a

´ = cos α ∗ a ≡ cosα´ =

a
a1

´ ∗ cos 20° ≡ α´ = arccos (

a
a1

´ ∗ cos 20°) (15)

α´ = arccos (

236,25
236 ∗ cos(20)) = 19,83 °
- α´ − novo ângulo de pressão de funcionamento [°]
- a

´ − entre eixo de funcionamento [mm]
- a − entre eixo normal [mm]

INV α

´ = INV α + 2 ∗ tan α ∗

X1+ X2
Z1+ Z2

(16)

tan(19,83) − 19,83 = tan(20) − 20 + 2 × tan(20) ×

X1 + X2
30 + 75

X1 + X2 =

(0,014521 − 0,014904) × 105
0,72794 | = −0,0553 mm
- X1 e X2 − valores mínimos da correção com variação de entre eixo [mm]

a

´ − a < (X1 + X2
) ∗ m | (17)

236 − 236,25 < −0,0553 × 4,5

−0,25 < −0,249

- Verificação da folga de engrenamento nula

X1 = λ ∗

u−1
u+1

+

X1+X2
u+1
[mm] | (18)

X1 = 0,5 ∗

2,5 − 1
2,5 + 1

+

−0,0553
2,5 + 1

= 0,198 mm

X2 = (X1 + X2

) − X1

[mm] | (19)

X2 = −0,0553 − 0,198 = −0,254 mm

- Seleção do desvio X1 e X2 no pinhão e na roda
- 0,5 ≤ λ ≤ 0,75 − engrenagens redutoras

Após achar os resultados das correções individuais determinaram-se os diâmetros exteriores das rodas dentadas no terceiro nível utilizando as equações 20 e 21. Estes diâmetros são necessários para calcular o novo diâmetro primitivo já corrigido, de onde se utilizou a equação 22.

Dexterior(Zpinℎão

) = D + 2 ∗ (m + X1 ∗ m) [mm] | (20)

Dexterior(Zpinℎão

) = 135 + 2 × (4,5 + 0,198 × 4,5) = 145,79 mm

- Dexterior(Zpinhão) − Diâmetro exterior do pinhão [mm]
- D − Diâmetro do pinhão [mm]
Dexterior(Zroda) = D + 2 ∗ (m + X2 ∗ m) [mm] | (21)

Dexterior(Zroda) = 337,5 + 2 × (4,5 − 0,254 × 4,5) = 344,22 mm

- Dexterior(Zroda) − Diâmetro exterior da roda [mm]
- D − Diâmetro da roda [mm]
Dp = Dexterior − 2 ∗ mn | (22)

Dppinℎão

= 145,79 − 2 × 4,5 = 136,79 mm

Dproda = 344,22 − 2 × 4,5 = 335,22 mm

- Dp − diâmetro primitivo

Os resultados que se obtiveram durante os cálculos dos diâmetros externos estão apresentados na tabela 6 bem como os novos diâmetros primitivos para as rodas dentadas da engrenagem do nível 3.

Tabela 6 – Novos diâmetros das engrenagens.

Nível da engrenagem | Diâmetro externo (De) | Diâmetro primitivo (D) | Diâmetro do pé (Dp) | Diâmetro da base (Db)
1 | 58/150 | Não se altera | Não se altera | Não se altera
2 | 91/209 | Não se altera | Não se altera | Não se altera
3 | 146/344 | 137/335 | 128/313 | 126/324

É importante salientar que, com estas correções, alteraram-se os valores de fator de concentração de tensões (YF) para 0,5, sendo que o módulo não variou significativamente para mudar o módulo normalizado obtido nos vários níveis de engrenagem.

Por fim, pode ver-se no esquema cinemático da figura 3 o resultado final do redutor dimensionalizado.

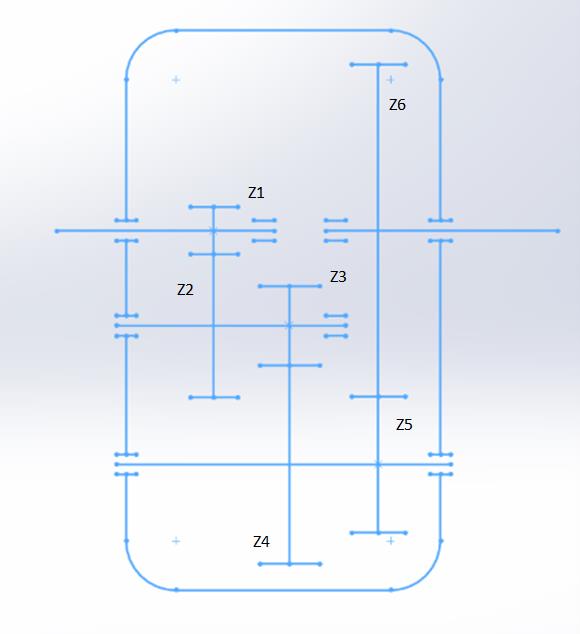
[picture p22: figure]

Figura 3 – Esquema cinemático final.

### Conclusão

Após o dimensionamento do redutor, as dimensões principais das engrenagens (diâmetros e largura) foram colocadas numa tabela final, a tabela 7.

Tabela 7 – Valores finais do tamanho das rodas dentadas.

Nível | Módulo [mm] | De [mm] | D [mm] | DP [mm] | Db [mm] | L [mm] | Lt [mm]
1 | 4 | 58/150 | 48/144 | 38/134 | 45/135 | 48 | 52
2 | 5 | 91/209 | 80/200 | 68/188 | 75/187 | 60 | 64
3 | 4,5 | 146/344 | 137/335 | 128/313 | 126/324 | 57 | 58

Destes resultados podem ser obtidas as dimensões teóricas do redutor, e analisando juntamente com o esquema cinemático, podemos chegar a uma conclusão de que este terá uma altura de 521 mm e uma largura de 165 mm. É de salientar que a solução de redutor apresentada e desenvolvida neste projeto não tem em conta, para já, as dimensões do cárter de alumínio nem dos componentes que complementam o redutor, como por exemplo os rolamentos, sendo que estes irão acrescentar mais largura.

De modo a verificar que o redutor dimensionado por nós se encontra dentro do normal no mercado, fomos verificar ao catálogo de redutores coaxiais da empresa Rexnord que, para um motor de 30 hp (≈22kw) e velocidade de rotação 1750 rpm, apresenta um redutor com uma altura de 435,8mm e uma largura de 401 mm.

Analisando as dimensões ideais do redutor desenvolvido neste projeto, podemos observar que a altura se situa a cerca de aproximadamente 90mm acima do desejado, sendo que esta ainda não tem em consideração a altura do cárter. Provavelmente as engrenagens poderiam ser dimensionadas de maneira diferente, reduzindo o número de dentes das rodas dentadas ou o seu módulo. No que toca à largura, não podemos chegar a uma conclusão definitiva sem saber quanto iriam ocupar elementos como rolamentos, veios, etc.

## PARTE 2

### Introdução

De modo a continuar com o dimensionamento do redutor de eixos paralelos com veio de entrada e saída coaxiais, transmitindo uma potência de 22 kW e usando um fator de redução de 18.75 (velocidade de entrada de 1500 rpm e velocidade de saída de 80 rpm), procedeu-se ao dimensionamento de rolamentos e de veios a utilizar, de modo a garantir a integridade estrutural do redutor e a sua funcionalidade.

Começou-se por identificar e calcular as forças aplicadas nos pares pinhão/roda e consequentemente nos veios dos mesmos, representando-as em esquemas.

De seguida determinou-se as reações presentes nos apoios dos veios sendo que se foram considerados 2 planos possíveis: OXY e OXZ. O cálculo destas reações foi feito através de um software chamado FTool. Este software apresenta cálculos precisos sobre o comportamento dos veios e inclusive permite uma boa organização no que toca à representação e armazenamento das forças para testes futuros.

Após termos as reações nos apoios, foi possível determinar as forças radiais e axiais aplicadas em cada rolamento sendo que com estas se procedeu ao cálculo dos fatores de carga C e C0, permitindo-nos escolher os rolamentos a usar, a partir dos catálogos dos fabricantes.

Através dos critérios de cedência (Tresca e Von Mises) e dos momentos fletor máximo e torsor, calculou-se o diâmetro mínimo para um fator de segurança de 1,5 que é comum no fabrico de redutores. Em função deste diâmetro procedeu-se então ao cálculo da flecha na zona de engrenamento e da rotação nos apoios dos veios usando também o software FTool.

Com estes valores, procedeu-se ao dimensionamento das chavetas e/ou veios estriados de modo que as engrenagens possam transmitir o momento torsor ao veio. No caso deste projeto foram dimensionadas chavetas para todos os veios e veio estriado para o lado direito do segundo veio.

Por fim, fez-se um esboço de cada veio e realizou-se o dimensionamento à fadiga para cada uma das secções de transição geométrica do mesmo.

### Identificação das forças de engrenamento aplicadas nos veios

Neste projeto, e como se pode ver no esquema cinemático da PARTE 1, o redutor irá possuir 4 veios sendo que estes precisam de ser dimensionados tendo em conta os esforços exercidos nos mesmos. Estes esforços são exercidos essencialmente pelas forças de engrenamento.

Quando referimos forças de engrenamento temos em mente três: força tangencial, força radial e força axial. A fórmula para calcular estas forças está representada pelas equações 23, 24 e 25 cujos resultados, para cada par pinhão/roda, são apresentados juntamente com essas equações.

Mt1 =

P
ω1
[Nm] | Ft1 =

Mt1
R1

=

2×Mt1
mt×Z1
[N] | (23)
Mt1 = 140,06 N. m | Ft1 =

140,06
24×10⁻³ = 5835,68 N
Mt2 = 420,16 N. m | Ft2 =

420,16
40×10⁻³ = 10504 N
Mt3 = 1050,42 N. m | Ft3 =

1050,42
68,5×10⁻³ = 15334,60 N

Mt4 = 2484,20 N. m

Fr1 = Ft1

tan(α)
cos(β)
[N] | (24)

Fr1 = 5835,68 ×

tan(20)
cos(20)

= 2260,33 N

Fr2 = 10504 ×

tan(20)
cos(20)

= 4068,50 N

Fr3 = 15334,60 ×

tan(20)
cos(20)

= 5939,54 N

Fa1 = Ft1 × tan(β) [N] | (25)

Fa1 = 5835,68 × tan(20) = 2124,01 N

Fa2 = 10504 × tan(20) = 3823,14 N

Fa3 = 15334,60 × tan(20) = 5581,34 N

- Ft1 − força tangencial de engrenamento [N]
- Fr1 − força radial de engrenamento [N]
- Fa − força axial de engrenamento [N]
- P − potência a transmitir pela engrenagem [W]
- Mt1 − momento torsor a transmitir pelo pinℎão [N m]
- ω1 − velocidade angular do pinℎão [
rad
s

]

- R1 − raio primitivo do pinℎão [m]
- mt − módulo aparente da engrenagem [m]
- Z1 − número de dentes do pinℎão [adimensional]
- α − ângulo de pressão [°]
- β − ângulo de ℎélice primitiva do dentado [°]

Estas forças serão importantes para calcular as reações presentes nos apoios dos veios e os momentos fletores máximos no local do engrenamento.

Isolando cada veio individualmente, podemos verificar como é que as forças tangenciais e radiais estão distribuídas pelo veio, bem como a dimensão dos mesmos considerando dois planos: OYX e OYZ.

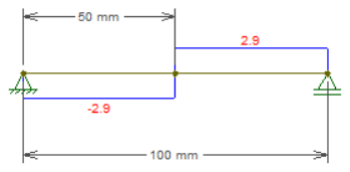
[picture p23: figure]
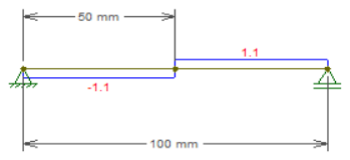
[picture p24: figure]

Resquerdo = 1,1 kN. mm | Resquerdo = 2,9 kN. mm
Rdireito = 1,1 kN. mm | Rdireito = 2,9 kN. mm

Figura 4 – Dimensões e forças aplicadas no veio 1: Plano OXY (esquerda) e Plano OXZ (direita).


Resquerdo = 0,1 kN. mm | Resquerdo = 0,3 kN. mm
Rdireito = 1,9 kN. mm | Rdireito = 5 kN. mm

Figura 5 – Dimensões e forças aplicadas no veio 2: Plano OXY (esquerda) e Plano OXZ (direita).


Resquerdo = 1 kN. mm | Resquerdo = 2,5 kN.mm
Rdireito = 2,8 kN. mm | Rdireito = 7,3 kN. mm

Figura 6 – Dimensões e forças aplicadas no veio 3: Plano OXY (esquerda) e Plano OXZ (direita).



Resquerdo = 2,9 kN. mm | Resquerdo = 7,6 kN. mm
Rdireito = 3,0 kN. mm | Rdireito = 7,7 kN. mm

Figura 7 – Dimensões e forças aplicadas no veio 4: Plano OXY (esquerda) e Plano OXZ (direita).

Através destes esquemas e das forças calculadas foi possível determinar as reações nos apoios que estão descritas juntamente com as imagens dos veios.

É de notar que os cálculos das reações foram realizados no software FTool como já foi referido na introdução.

### Dimensionamento de Rolamentos

Para fazer o dimensionamento dos rolamentos começou-se por calcular as forças de reação nos apoios do veio.

As forças axiais apresentadas nos apoios foram consideradas como sendo a soma das forças axiais de engrenamento.

Como nos apoios teremos presentes tanto forças radiais como forças axiais, inicialmente optaram-se por escolher rolamentos de contacto angular de esferas carreira simples. Escolhida a suposição inicial, passou-se para a determinação dos fatores de carga. Para isso, recorreu-se às seguintes equações, de onde os resultados estão presentes logo a seguir. É importante salientar que se considerou que os veios irão ter os mesmos rolamentos tanto no lado esquerdo como no lado direito.

P0 = X0 × Fr + Y0 × Fa [kN] | (26)

C0 = fs × P0

[kN] | (27)

P01 = 0,5 × 2260,33 + 0,38 × 2124,01 = 1937,29 N = 1,94 kN

C01 = 1,5 × 1937,29 = 2905,93 N = 2,91 kN

P02 = 0,5 × 4068,50 + 0,38 × 3823,14 = 3487,05 N = 3,49 kN

C02 = 1,5 × 3487,05 = 5230,57 N = 5,23 kN

P03 = 0,5 × 5939,54 + 0,38 × 5581,34 = 5090,68 N = 5,09 kN

C03 = 1,5 × 5090,68 = 7636,01 N = 7,64 kN

P04 = 0,5 × 5939,54 + 0,38 × 5581,34 = 5090,68 N = 5,09 kN

C04 = 1,5 × 5090,68 = 7636,01 N = 7,64 kN

- C0 − capacidade de carga estática [kN]
- fs − coeficiente de segurança [adimensional]
- P0 − carga estática equivalente [kN]
- X0 − fator radial [adimensional]
- Y0 − fator axial [adimensional]
P = X × Fr + Y × Fa [kN] | (28)

C =

fl
fn×ft
× P [kN] | (29)

P1 = 0,41 × 2260,33 + 0,87 × 2124,01 = 2774,63 N = 2,77 kN

C1 =

2
0,281 × 1

× 2774,63 = 19748,24 N = 19,75 kN

P2 = 0,41 × 4068,50 + 0,87 × 3823,14 = 4994,22 N = 4,99 kN

C2 =

2
0,405 × 1

× 4994,22 = 24662,82 N = 24,66 kN

P3 = 0,41 × 5939,54 + 0,87 × 5581,34 = 7290,97 N = 7,29 kN

C3 =

2
0,405 × 1

× 7290,97 = 36004,80 N = 36,00 kN

P4 = 0,41 × 5939,54 + 0,87 × 5581,34 = 7290,97 N = 7,29 kN

C4 =

2
0,693 × 1

× 7290,97 = 21041,77 N = 21,04 kN

- C − capacidade de carga dinâmica [kN]
- fn − fator de rotação [adimensional]

- fl − fator de esforços dinâmicos [adimensional]
- fl − fator de temperatura [adimensional]
- P − carga dinâmica equivalente [kN]
- X − fator radial [adimensional]
- Y − fator axial [adimensional]
- Fr − carga radial [kN]
- Fa − carga axial [kN]

Tabela 8 – Valores dos fatores de carga estática e dinâmica.

| Veio 1 | Veio 2 | Veio 3 | Veio 4
X0 | 0,5 | 0,5 | 0,5 | 0,5
Y0 | 0,38 | 0,38 | 0,38 | 0,38
X | 0,41 | 0,41 | 0,41 | 0,41
Y | 0,87 | 0,87 | 0,87 | 0,87

Na tabela 9 encontram-se as características e os números dos rolamentos selecionados no catálogo da KOYO (2).

Tabela 9 – Características dos rolamentos selecionados.

| Calculado | Rolamentos selecionados
C0 (kN) | C (kN) | KOYO | C0 (kN) | C (kN) | d (mm) | D (mm) | b (mm) | r (mm) | nmax (rpm) massa/ óleo
Veio 1 | Esquerdo | 2,91 | 19,75 | 7304C * | 11,1 | 19,9 | 20 | 52 | 15 | 1,1 | 23000/ 31000
| Direito | = | = | = | = | = | = | = | = | = | =
Veio 2 | Esquerdo | 5,23 | 24,66 | 7404B # | 17,9 | 33,5 | 20 | 72 | 19 | 1,1 | 8500/1200
| Direito | = | = | = | = | = | = | = | = | = | =
Veio 3 | Esquerdo | 7,64 | 36,00 | 7405B * | 23,9 | 39,6 | 25 | 80 | 21 | 1,5 | 7300/ 10000
| Direito | = | = | = | = | = | = | = | = | = | =
Veio 4 | Esquerdo | 7,64 | 21,04 | 7305B # | 13,3 | 22,9 | 25 | 62 | 17 | 1,1 | 10000/ 14000
| Direito | = | = | = | = | = | = | = | = | = | =

# with machined cage

* with pressed cage

Todos os rolamentos selecionados através do catálogo da KOYO garantem o diâmetro mínimo compatível com o mecanismo, inclusive, quando montados não irão interferir com a montagem dos outros veios.

### Dimensionamento do veio – Critério de cedência

De modo a garantir a segurança e durabilidade do redutor, em primeiro lugar, realizou-se o dimensionamento do diâmetro mínimo que o veio deverá ter. Para isso recorreu-se aos dois critérios de cedência conhecidos: Tresca e Von Mises, sendo que se escolheu o que garantia um diâmetro mínimo maior entre estes. Para calcular estes dois critérios, teve-se em consideração a tensão normal máxima e a tensão de corte máxima como demonstram as equações 30 e 31.

(σbmax)i =

32Mb(x)
πDi

3

(30)

- σbmax − tensão normal máxima
- Mb
(x) − momento flector
- Di − diâmetro

(τtmax)i =

16Mt(x)
πDi

3

(31)

- τtmax − tensão de corte máxima
- Mt
(x) − momento torsor

Como se pode observar, estas equações dependem tanto do momento torsor como do momento fletor. O momento torsor pode ser calculado através da equação 32 e da qual se obteve os resultados abaixo para cada veio.

T =

P
π.

ω
60

(32)

T1 = 140,06 N. m

T2 = 420,16 N. m

T3 = 1050,42 N. m

T4 = 2484,20 N. m

- T – Momento torsor (N m)
- P – Potência (W)
- ω – Velocidade do veio (rpm)

Já o momento fletor foi calculado através do software FTool, de onde se pode ver os resultados abaixo nas figuras 8,9,10 e 11, tanto nos planos OXY e OXZ.


Figura 8 – Diagrama de momentos (kN.mm) no veio 1: Plano OXY (esquerda) e Plano OXZ (direita).

Figura 9 – Diagrama de momentos (kN.mm) no veio 2: Plano OXY (esquerda) e Plano OXZ (direita).

Figura 10 – Diagrama de momentos (kN.mm) no veio 3: Plano OXY (esquerda) e Plano OXZ (direita).

Figura 11 – Diagrama de momentos (kN.mm) no veio 4: Plano OXY (esquerda) e Plano OXZ (direita).

Tendo estes dois valores procedeu-se então primeiro ao cálculo do critério de Tresca. Este pode ser visto na equação 33, bem como, a seguir, o seu resultado.

√σbmax
2 + 4 × τtmax

2 ≤

σy
γ

; √(
16Mb(x)
πDi

3 )

2
+ (
16Mt(x)
πDi

3 )

2
≤

σy
2 × γ

Di ≥ √
32 × γ
π × σy

√Mb
(x)

2 + Mt
(x)

2

3
[mm] | (33)

D1 ≥ √
32 × 1,5
π × 750 √(155,80 × 10³)
2 + (140,06)

2

3
≥ 14,7 mm

D2 ≥ √
32 × 1,5
π × 750 √(303,99 × 10³)
2 + (420,16)

2

3
≥ 18,4 mm

D3 ≥ √
32 × 1,5
π × 750 √(439,03 × 10³)
2 + (1050,42)

2

3
≥ 20,8 mm

D4 ≥ √
32 × 1,5
π × 753 √(430,85 × 10³)
2 + (2484,20)

2

3
≥ 20,6 mm
- σbmax − tensão normal máxima
- τtmax − tensão de corte máxima
- Mb

(x) − momento flector
- Mt

(x) − momento torsor
- Di − diâmetro mínimo
- σy − tensão de cedência do material
- γ − fator de segurança

Por fim, recorreu-se ao critério de Von Mises usando a equação 34, obtendo-se os resultados abaixo indicados.

√(σbmax)
2 + 3 × τtmax

2 ≤

σy
γ

Di ≥ √
32 × γ
π × σy

√Mb
(x)

2 + 0,75 × Mt
(x)

2

3
[mm] | (34)

D1 ≥ √
32 × 1,5
π × 750 √(155,80 × 10³)
2 + 0,75 × (140,06)

2

3
≥ 14,7 mm

D2 ≥ √
32 × 1,5
π × 750 √(303,99 × 10³)
2 + 0,75 × (420,16)

2

3
≥ 18,4 mm

D3 ≥ √
32 × 1,5
π × 750 √(439,03 × 10³)
2 + 0,75 × (1050,42)

2

3
≥ 20,8 mm

D4 ≥ √
32 × 1,5
π × 750 √(430,85 × 10³)
2 + 0,75 × (2484,20)

2

3
≥ 20,6 mm
- σbmax − tensão normal máxima
- τtmax − tensão de corte máxima
- Mb

(x) − momento flector
- Mt

(x) − momento torsor
- Di − diâmetro mínimo
- σy − tensão de cedência do material
- γ − fator de segurança

Fazendo agora uma comparação com os valores tanto do critério de Tresca como o de Von Mises, e tendo em consideração as séries de Renard como critério de normalização, chegou-se a conclusão de que os diâmetros mínimos dos veios serão os seguintes:

Dveio1 = 20 mm

Dveio2 = 20 mm

Dveio3 = 25 mm

Dveio4 = 25 mm

É importante salientar que estes diâmetros já dispõem de correções eventuais futuras. Sendo que os diâmetros que foram escolhidos inicialmente não passavam nos critérios de fadiga.

### Dimensionamento do veio – Critério de Rigidez

Para avaliar a rigidez do veio, tem-se em consideração o diâmetro mínimo e o material utilizado. Para determinar se o veio é rígido o suficiente, mediu-se a flecha nos pontos de engrenamento e a rotação nos apoios. Nesta medição recorreu-se ao software FTool.


Figura 12 – Diagramas de flecha (mm) (esquerda) e de rotação (rad) (direita) no veio 1: Plano OXY.

Figura 13 – Diagramas de flecha (mm) (esquerda) e de rotação (rad) (direita) no veio 2: Plano OXY.

Figura 14 – Diagramas de flecha (mm) (esquerda) e de rotação (rad) (direita) no veio 3: Plano OXY.

Figura 15 – Diagramas de flecha (mm) (esquerda) e de rotação (rad) (direita) no veio 4: Plano OXY.

Os resultados da flecha e da rotação são apresentados na tabela 10:

Tabela 10 – Valores da rotação e flecha de cada veio.

Rotação (°) / Flecha (mm) | Valor (máx) | Limite | Verificação
Veio 1 | Rotação | 0,0498 | 3 | ok
| Flecha | 0,0292 | 0,15 | ok
Veio 2 | Rotação | 0,1361 | 3 | ok
| Flecha | 0,1060 | 0,15 | ok
Veio 3 | Rotação | 0,0595 | 3 | ok
| Flecha | 0,0380 | 0,15 | ok
Veio 4 | Rotação | 0,0580 | 3 | ok
| Flecha | 0,0353 | 0,15 | ok

Como podemos ver, todos os veios passam no critério de rigidez sendo que não é preciso sofrerem alterações de correção.

### Dimensionamento de chavetas / veios estriados

De modo a conseguir transmitir o momento torsor da engrenagem para os veios, é necessário dimensionar chavetas ou veios estriados.

No caso do nosso projeto, o dimensionamento foi feito quase na totalidade para chavetas, apenas o segundo veio necessitou de ser veio estriado do lado direito, uma vez que para o dimensionamento dessa chaveta não houve correspondência com os critérios.

O dimensionamento de chavetas relaciona-se com a resistência ao corte do material da chaveta (τa adm) e também com a resistência à compressão-esmagamento desse material
(σd adm).

Assim para começar a fazer o dimensionamento definiu-se a tensão de corte admissível como 100 MPa, pois esta varia entre 70 e 100 MPa, sendo o valor máximo entre estes para situações em que a solicitação seja constante. Já para a tensão de esmagamento admissível foi selecionado, através da tabela 6.2 do livro (1), o valor de 110 MPa.

De seguida, tendo em consideração o diâmetro de cada veio e após a consulta da tabela 6.1 do livro (1) com as dimensões das chavetas paralelas, podemos determinar as dimensões das chavetas para cada diâmetro de cada veio.

O passo seguinte foi, através das equações 35 e 36, ver se as condições de resistência ao corte e ao esmagamento se verificaram e assim determinar o comprimento mínimo da chaveta (L).

O comprimento do cubo (lc) deve ser 10 mm mais longo do que o comprimento da chaveta e também deve ser menor do que 2,5 vezes o diâmetro, se for superior é melhor escolher uma secção estriada.

Os cálculos realizados podem ser vistos abaixo e todos os valores selecionados na tabela 6.1 do livro (1) e obtidos nos cálculos encontram-se na tabela 11.

τa =

2×Mt
L × b ×d

< τa adm [N/m²
] | (35)

L >

2 × Mt
τa adm × b × d

[m]

* | L − comprimento útil da cℎaveta [m]
* | Mt − momento torsor [N m]
* | τa − tensão de corte [N/m² ]
* | b − largura da cℎaveta [m]
* | d − diametro do veio [m]

L veio 1 acopolamento >

2 × 140,06
100 × 10⁶ × 6 × 10⁻³ × 16 × 10⁻³ = 0,00292 m = 2,9 mm

Lveio 1 pinℎão >

2 × 140,06
100 × 10⁶ × 6 × 10⁻³ × 20 × 10⁻³ = 0,00233 m = 2,3 mm

L veio 2 roda >

2 × 420,16
100 × 10⁶ × 6 × 10⁻³ × 20 × 10⁻³ = 0,00700 m = 7,0 mm

Lveio 2 pinℎão >

2 × 420,16
100 × 10⁶ × 6 × 10⁻³ × 20 × 10⁻³ = 0,00700 m = 7,0 mm

Lveio 3 roda >

2 × 1050,42
100 × 10⁶ × 8 × 10⁻³ × 25 × 10⁻³ = 0,01050 m = 10,5 mm

Lveio 3 pinℎão >

2 × 1050,42
100 × 10⁶ × 8 × 10⁻³ × 25 × 10⁻³ = 0,01050 m = 10,5 mm

Lveio 4 roda >

2 × 2484,20
100 × 10⁶ × 8 × 10⁻³ × 25 × 10⁻³ = 0,02484 m = 24,8 mm

Lveio 4 acopolamento >

2 × 2484,20
100 × 10⁶ × 8 × 10⁻³ × 25 × 10⁻³ = 0,03943 m = 39,4 mm

σd =

2×Mt
L×d×(ℎ−t1)

< σd adm [N/m²
] | (36)

L >

2 × Mt
σd adm × d × (ℎ − t1)

[m]

* | L − comprimento útil da cℎaveta [m]
* | Mt − momento torsor [N m]
* | σd − tensão de esmagamento [N/m² ]
* | d − diametro do veio [m]

L veio1 acopolamento >

2 × 140,06
110 × 10⁶ × 16 × 10⁻³ × (6 × 10⁻³ − 3,5 × 10⁻³)

= 0,00637 m = 6,4 mm

Lveio 1 pinℎão >

2 × 140,06
110 × 10⁶ × 20 × 10⁻³ × (6 × 10⁻³ − 3,5 × 10⁻³)

= 0,00509 m = 5,1 mm

L veio 2 roda >

2 × 420,16
110 × 10⁶ × 20 × 10⁻³ × (6 × 10⁻³ − 3,5 × 10⁻³)

= 0,01528 m = 15,3 mm

Lveio 2 pinℎão >

2 × 420,16
110 × 10⁶ × 20 × 10⁻³ × (6 × 10⁻³ − 3,5 × 10⁻³)

= 0,01528 m = 15,3 mm

Lveio 3 roda >

2 × 1050,42
110 × 10⁶ × 25 × 10⁻³ × (7 × 10⁻³ − 4 × 10⁻³)

= 0,02547 m = 25,5 mm

Lveio 3 pinℎão >

2 × 1050,42
110 × 10⁶ × 25 × 10⁻³ × (7 × 10⁻³ − 4 × 10⁻³)

= 0,02547 m = 25,5 mm

Lveio 4 roda >

2 × 2484,20
110 × 10⁶ × 25 × 10⁻³ × (7 × 10⁻³ − 4 × 10⁻³)

= 0,06022 m = 60,2 mm

Lveio 4 acopolamento >

2 × 2484,20
110 × 10⁶ × 21 × 10⁻³ × (6 × 10⁻³ − 3,5 × 10⁻³)

= 0,08603 m = 86,0 mm

Tabela 11 – Dimensionamento das chavetas.

| Zona engrenamento | d | b | h | t1 | t2 | Lmin | Lmax | L | Lcubo | 2,5*d | τaadm | σd adm
Veio 1 | 1 (acoplamento) | 16 | 6 | 6 | 3,5 | 2,8 | 14 | 70 | 40 | 50 | 40 | 100 | 110
| 2 | 20 | 6 | 6 | 3,5 | 2,8 | 14 | 70 | 38 | 48 | 50 | 100 | 110
Veio 2 | 1 | 20 | 6 | 6 | 3,5 | 2,8 | 14 | 70 | 38 | 48 | 50 | 100 | 110
| 2 | 20 | 6 | 6 | 3,5 | 2,8 | 14 | 70 | 50 | 60 | 50 | 100 | 110
Veio 3 | 1 | 25 | 8 | 7 | 4 | 3.3 | 18 | 90 | 50 | 60 | 62,5 | 100 | 110
| 2 | 25 | 8 | 7 | 4 | 3.3 | 18 | 90 | 44 | 54 | 62,5 | 100 | 110
Veio 4 | 1 | 25 | 8 | 7 | 4 | 3.3 | 18 | 90 | 44 | 54 | 62,5 | 100 | 110
| 2 (acoplamento) | 21 | 6 | 6 | 3,5 | 2,8 | 18 | 90 | 40 | 50 | 52,5 | 100 | 110

*todas unidades da tabela são em mm, à exceção das τaadm e σd adm que são em N/m²

Como na zona 2 (lado direito) do veio 2 o L do cubo é superior ao superior a 2,5 vezes o diâmetro devemos utilizar aqui um veio estriado.

Para fazer o dimensionamento de veios estriados começou-se por, através da tensão de esmagamento admissível (que foi considerada como 110 MPa), determinar o comprimento mínimo útil da estria. Através da equação abaixo obtiveram-se os resultados mostrados.

σd =

2×Mt×Kt
(

D+d
2

×z×ℎ×L)

< σd adm [N/m²
] (35)

O h, altura útil de contacto das estrias, pode ser estimada como 0,75 da altura efetiva da estria ((D-d)/2).

Para as dimensões normalizadas escolhidas na tabela 6.4 do (1), secção estriada média 6 × 18 × 22:

L1 >

2 × 140,05
(

21 + 25
2

× 6 × 1,5 × 110)

= 0, mm

* | σd − tensão de esmagamento [N/m² ]
* | D − diametro exterior do veio − estriado [m]
* | d − diametro interior do veio − estriado [m]
* | Mt − Momento torsor [N m]
* | L − comprimento útil da estria [m]
* | ℎ − altura útil de contacto das estrias [m]
* | z − número de estrias [adimensional]
* | Kt − fator de irregularidade de carga entre estrias [adimensional]

Sendo que estes valores obtidos para o comprimento útil da estria terão de corresponder à relação dada pela equação abaixo apresentada.

L < 1,5 ∗ d (36)

L1 < 1,5 ∗ 21 < 30,5 mm

O valor dos veios estriados obtidos para cada roda são os da tabela 11.

Tabela 12 – Dimensionamento veios estriados.

Zona engrenamento | P(kW) | n (rpm) | z | d | D | h | kt | b | L | σadm
Veio 1 | 1 | 22 | 1500 | 6 | 28 | 32 | 1,5 | 1,5 | 7 | 42 | 100
Veio 2 | 1 | 22 | 500 | 8 | 32 | 36 | 1,5 | 1,5 | 7 | 42 | 100
| 2 | 22 | 500 | 8 | 36 | 40 | 2 | 1,1 | 7 | 56 | 110
Veio 3 | 1 | 22 | 200 | 8 | 42 | 46 | 2 | 1,1 | 8 | 54 | 100
| 2 | 22 | 200 | 8 | 42 | 46 | 1,5 | 1,1 | 8 | 48 | 100

Veio 4 | 1 | 22 | 80 | 8 | 56 | 62 | 3 | 1,1 | 10 | 48 | 100

### Esboços dos veios

Recorrendo a todos os dimensionamentos foi possível desenhar os primeiros esboços dos veios a usar no redutor. Para isso, recorreu-se ao software SolidWorks sendo que se obtiveram os seguintes resultados.


Figura 16 – Esboço do veio 1.


Figura 17 – Esboço do veio 2.


Figura 18 – Esboço do veio 3.


Figura 19 – Esboço do veio 4.
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

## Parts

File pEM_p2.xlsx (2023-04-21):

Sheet: Dados
Dados dos Problema
Capacidade de Carga | 250 | kg
Área Elevação | 0.5 | m2
Capacidade Elevação | 12 | m
Velocidade Elevação | 35 | m/min | 0.58 | m/s
 |  |  |  |  | Definição e dimensionamento da transmissão / sistema motriz
 |  |  |  |  | Desenho de grande fiabilidade e elevado rendimento
 |  |  |  |  | Dimensionar/Verificar rodos componentes (esforços)
 |  |  |  |  | (engrenagens,veios,rolamentos,chavetas,estrutura suporte..)
 |  |  |  |  | Desenho de conjunto comprrender a construção maquina
 |  |  |  |  | Simulação com MEF os principais elementos estruturais

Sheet: Cabo aço V.2
caracteristicas |  |  |  |  |  |  |  |  |  |  |  |  | Flexibilidade | Tracao | E [Gpa] |  | Classificação | E min [Gpa]
H máximo | 12 | m |  |  |  |  |  |  | 2452.5 |  | AF/AFA | Alma de fibra | + | - | 65 - 100 | AF/AFA | 6x7 | 90
L Comp. Cabo | 26 | m |  |  |  |  |  |  |  |  | AA e AACI | Alma de aço | - | + | 95 - 115 |  | 6x19 | 85
Carga Real [F] | 2452.5 | N |  |  |  |  |  |  |  |  |  |  |  |  |  |  | 6x37 | 75 |  | Dimensoes Tambor cabo aço
Factor Segurança (Fs) | 5 |  |  |  |  |  | Especificação cabo de aço |  | Ø cabo x nº pernas x nº arames p/ perna + tipo alma |  |  |  |  |  |  |  | 8x19 | 65
Carga x Fs | 1250 | Kg |  |  |  |  |  |  |  |  |  |  |  |  |  | AA e AACI | 6x17 | 105 |  | https://electrolift.com/product/drums/
 |  |  |  |  |  |  |  |  |  |  |  |  |  |  |  |  | 6x19 | 100
 |  |  |  |  |  |  |  |  |  |  |  |  |  |  |  |  | 6x37 | 95 |  | Ø | 12" | 304.8 | mm
Tensão Rotura | 1770 | Mpa |  |  |  |  |  |  |  |  | carga trabalho
 |  |  |  |  |  | Rotura teorica |  | tensao rotura x A cabo |  |  | 1/5 carga rotura
 |  |  |  |  |  |  |  |  |  |  |  |  |  |  |  |  |  |  |  | Cabo de aço
 |  |  |  |  |  |  | 1770 | 1960
 |  |  |  |  |  |  |  |  |  |  |  |  |  |  |  |  |  |  |  | Ø
 |  | tipo |  | Ø [m] |  | área cabo | δ | Carga Rutura min / Fs | Am [m2] | ΔL | Ø Tambor | Ø Tambor
 |  | 1x7 |  | 0.004 |  | 1.256637061e-05 | 195.163749 | 2.74 | 9.536e-06 | 0.033 |  | x
 |  | 1x19 |  | 0.004 |  | 1.256637061e-05 | 195.163749 | 2.64 | 9.28e-06 | 0.034 |  | x
 |  | 6x19 |  | 0.007 |  | 3.848451001e-05 | 63.72693844 | 5.4 | 1.9355e-05 | 0.016 |  | 0.238
 |  | 6x25 |  | 0.008 |  | 5.026548246e-05 | 48.79093724 | 8.2 | 2.592e-05 | 0.012 |  | 0.312
 |  | 6x36 |  | 0.014 |  | 0.00015393804 | 15.93173461 | 10.3 | 7.938e-05 | 0.0040 | 0.476 | 0.322
 |  | Classificação | Classe | Ø [m] | E [Gpa] | Area cabo [m2] | δ | Carga de Trabalho [kN] | Am [m2] | ΔL [m] | Ø Tambor | L Tambor
 |  | 1x19 | Cordão | 0.004 |  | 1.256637061e-05 | 195.163749 | 3.00 | 9.28e-06 | 0.11
Guincho Obra |  | 6x25 | AACI | 0.008 | 105 | 5.026548246e-05 | 48.79093724 | 8.31 | 2.592e-05 | 0.01
Guindastes Gruas |  | 6x25 | Filler + AACI | 0.008 | 105 | 5.026548246e-05 | 48.79093724 | 8.31 | 2.592e-05 | 0.003709639126
Uso Geral |  | 6x25 | Filler + AF | 0.008 | 85 | 5.026548246e-05 | 48.79093724 | 7.73 | 2.592e-05 | 0.00
ESCOLHIDO : DEFINIDO: FABRICANTE LUIZ GODINHO
 |  |  |  |  |  |  |  |  |  |  |  |  |  |  |  |  |  |  | https://www.raseq.com/wire-rope/6x25-filler-wire-with-iwrc/
 |  |  |  |  |  |  |  |  |  |  |  |  |  |  |  |  |  |  | https://www.caboscar.com.br/cabos-de-aco
Guincho
Carga | 250 | kg
Factor Segurança | 5
Carga Real | 1250 | kg
Cabo | Ø [m]
6x7 CF | 0.005
 |  | Classificação | Classe | Ø [m] | E [Gpa] | Area cabo [m2] | δ | Carga de Trabalho [kN] | Am [m2] | ΔL [m] | Ø Tambor [m] | L Tambor
 |  | 6x7 | CF | 0.005 | 90.000 | 1.963495408e-05 | 124.9047993 | 3.00 | 9.5e-06 | 0.3725146199 | 0.36 | 0.22

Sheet: tambor_nervuras V2
 |  |  |  |  |  | B = diameter of groove diâmetro da ranhura= 1.06 x d
 |  |  |  |  |  | A = elevation of groove elevação da ranhura = 1.08 x d |  | For drums without rope grooves: |  |  | and 20 x drum width ~ ß = 1.5º.
 |  |  |  |  |  | C = depth of groove profundidade da ranhura = 0.30 x d |  | Lmin = 20 x drum width.
 |  |  |  |  |  | R = upper radius raio superior = approx. 0.15 x d
 |  |  |  |  |  | 2*pi*r |  |  |  |  | 15 x drum width ~ ß = 2º,
DIMENSIONAMENTO DO TAMBOR |  |  |  |  |  |  |  |  |  | TAMBOR DO MERCADO
 |  |  |  |  |  |  |  |  |  | FORNECEDOR | https://electrolift.com/product/drums/
 | L cabo total | 26 | m |  | For drums with rope grooves: |  |  |  |  | MODELO | M-358-P2
 | Ø cabo 6x7 CF | 0.005 | m |  | Lmin = 15 x drum width. |  |  |  |  | L tambor | 0.22 | m | Nº Voltas | 23.5
 | Ø tambor | 0.36 | m |  | Lmin | 1.9 | m |  |  | L min polia | 3.2 | m
 | Perímetro | 1.131 | m
 | Nº Voltas | 22.98904734
 |  |  |  |  |  |  |  |  |  |  |  |  | For drums with rope grooves:
 |  |  |  |  |  |  |  |  |  |  | 20 1/2" |  | Lmin = 15 x drum width.
 |  |  |  |  | A | 0.005 | m
 |  |  |  |  | B | 0.005 | m
 |  |  |  |  | C | 0.002 | m
 |  |  |  |  | R | 0.001 | m
 |  |  |  |  | L tambor | 0.13 | m
 |  |  |  |  |  |  |  |  | https://www.randers-reb.com/fishing-rope/rope-technology/handling-inspection-and-installation
 |  |  |  | Ø

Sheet: Cabo aço
 |  |  |  |  |  |  |  |  | Dimensoes Tambor cabo aço
 | H máximo | 12 | m |  | F | 2452.5 |  | N
 | L Comp. Cabo | 26 | m |  |  |  |  |  | https://electrolift.com/product/drums/
 |  | 26000 | mm
 |  |  |  |  |  |  |  |  | Ø | 12" | 304.8 | mm
 |  |  |  | 2450
Factor Segurança |  |  |  | 58800 |  |  |  |  | Cabo de aço
Fs | 5
 |  |  |  |  |  |  |  |  | Ø
Classificação | Ø [m] | área cabo | δ | Carga Rutura min / Fs | Am [m2] | ΔL | Ø Tambor | Ø Tambor
1x7 | 0.004 | 1.256637061e-05 | 195.163749 | 2.74 | 9.536e-06 | 0.033 |  | x
1x19 | 0.004 | 1.256637061e-05 | 195.163749 | 2.64 | 9.28e-06 | 0.034 |  | x
6x19 | 0.007 | 3.848451001e-05 | 63.72693844 | 5.4 | 1.9355e-05 | 0.016 |  | 0.238
6x25 | 0.008 | 5.026548246e-05 | 48.79093724 | 8.2 | 2.592e-05 | 0.012 |  | 0.312
6x36 | 0.014 | 0.00015393804 | 15.93173461 | 10.3 | 7.938e-05 | 0.0040 | 0.476 | 0.322
 |  |  |  | https://www.raseq.com/wire-rope/6x25-filler-wire-with-iwrc/
 |  |  |  | Fornecedor | RASEQ | 6x25 Filler

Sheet: tambor_nervuras
 |  |  |  |  | B = diameter of groove diâmetro da ranhura= 1.06 x d
 |  |  |  |  | A = elevation of groove elevação da ranhura = 1.08 x d |  |  |  |  | For drums without rope grooves: |  | and 20 x drum width ~ ß = 1.5º.
 | i.e. |  |  |  | C = depth of groove profundidade da ranhura = 0.30 x d |  |  |  |  | Lmin = 20 x drum width.
cabo L | 26 | m |  |  | R = upper radius raio superior = approx. 0.15 x d
cabo Ø | 0.014 | m |  |  |  |  |  | For drums with rope grooves: |  |  |  | 15 x drum width ~ ß = 2º,
tambor Ø | 0.476 | m |  | 2*pi*r |  |  |  | Lmin = 15 x drum width.
 |  |  | Perímetro | 1.495 | m |  |  | Lmin | 4.2
Nº Voltas | 17.38667446 | un
A | 0.015 | m
B | 0.015 | m
C | 0.004 | m
R | 0.002 | m
L tambor | 0.28 | m
 |  |  |  |  |  | A | 0.015 | m
 |  |  |  |  |  | B | 0.015 | m
 |  |  |  |  |  | C | 0.004 | m
 |  |  |  |  |  | R | 0.002 | m |  |  | https://www.randers-reb.com/fishing-rope/rope-technology/handling-inspection-and-installation
 |  |  | Ø

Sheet: Benchmarking
Easy Big WH-KI
Capacidade Máxima | 250 | kg
Alcance | 5,25 - 24 | m
Alcance sem articulação | 18 | m
Extensão | 3,5 -6,5 | m
Peso total | 1600 | kg
Comprimento | 6650 | mm
Largura | 1800 | mm
Rotação | 360 | º
Motor Gasolina Honda | 13 cv
Características
Articulação de joelho e Sist. Hidráulico
Travões de Disco multiplos / Guincho Elevação
Reboque amovivel
Controlo Remoto

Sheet: Motor Freio Specs
 | Motores Elétricos Trifásicos IEC com freio DC - Série BCL
 | Fabricante | Bernati
Série | BCL |  | P | 1.5 | Kw
 |  |  | n | 1500 | rpm
 |  |  | f | 50 | Hz
 |  |  | Polos | 4
 |  |  | IP65
 |  |  | Freio | DC

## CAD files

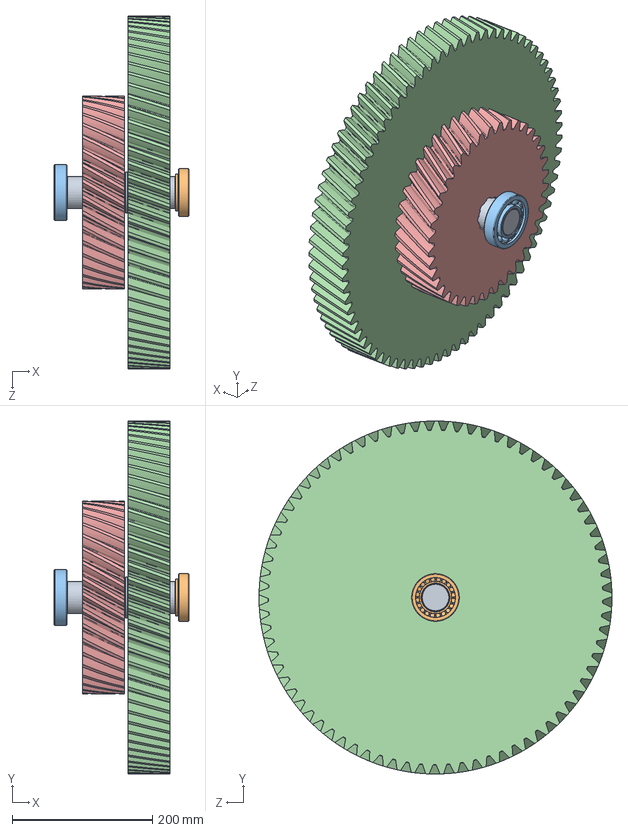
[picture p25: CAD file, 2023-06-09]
CAD_FINAL/CAD/Montagem_veio_3.SLDASM
192.0 x 503.6 x 503.6 mm
Veio_3
taper roller bearing_skf
angular contact ball bearing_68_skf
Z4
Z5

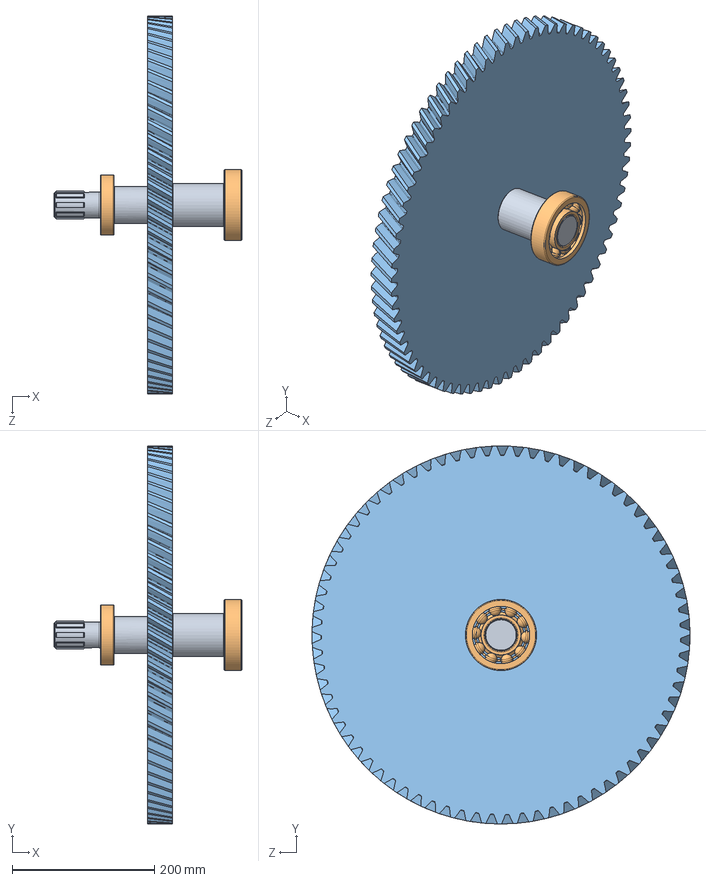
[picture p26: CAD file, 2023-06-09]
CAD_FINAL/CAD/Montagem_veio_4.SLDASM
264.0 x 531.5 x 531.6 mm
Veio_4
angular contact ball bearing_68_skf x 2
Z6

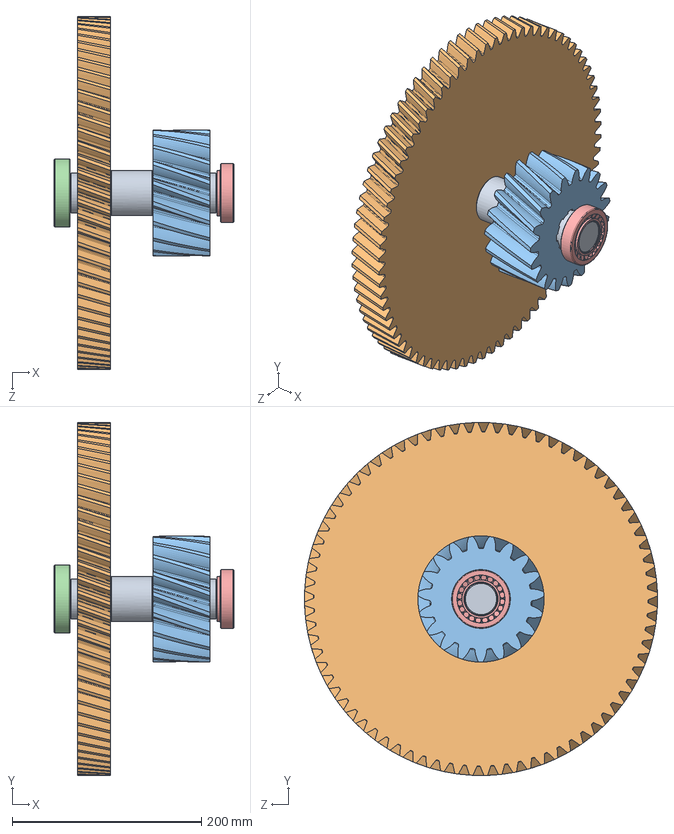
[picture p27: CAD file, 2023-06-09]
CAD_FINAL/CAD/Montagem_veio_2.SLDASM
190.0 x 372.9 x 372.9 mm
Veio_2
Z2
Z3
angular contact ball bearing_68_skf
taper roller bearing_skf

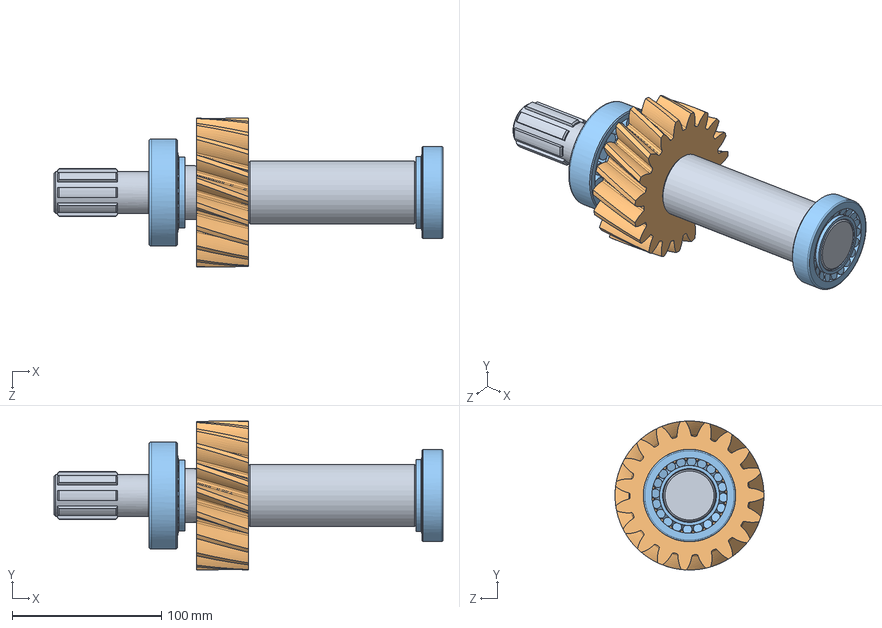
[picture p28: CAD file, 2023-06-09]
CAD_FINAL/CAD/Montagem_veio_1.SLDASM
261.0 x 99.9 x 99.9 mm
Veio_1
Z1
taper roller bearing_skf x 2

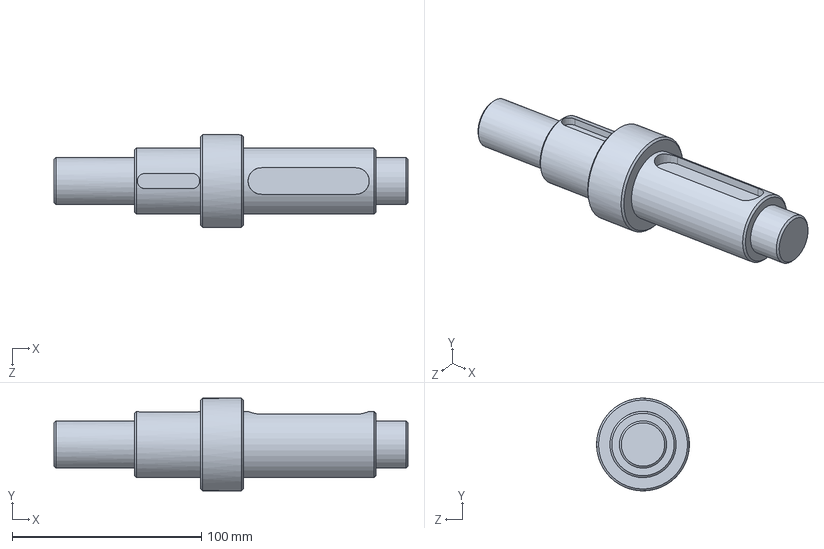
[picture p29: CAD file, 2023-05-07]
Veio_2.SLDPRT
187.0 x 49.0 x 49.0 mm

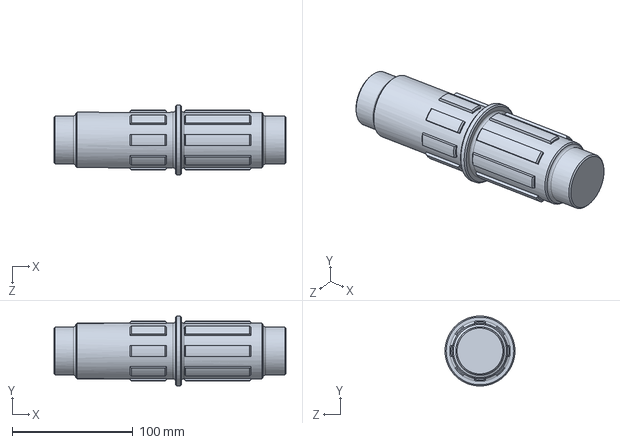
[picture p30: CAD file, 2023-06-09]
CAD_FINAL/CAD/Veio_3.SLDPRT
192.0 x 57.8 x 58.0 mm

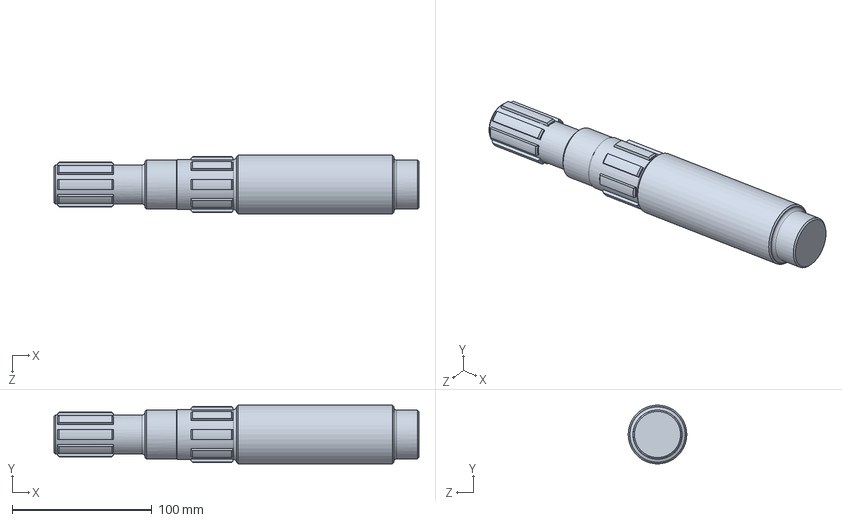
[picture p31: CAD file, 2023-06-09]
CAD_FINAL/CAD/Veio_1.SLDPRT
261.0 x 41.9 x 42.0 mm

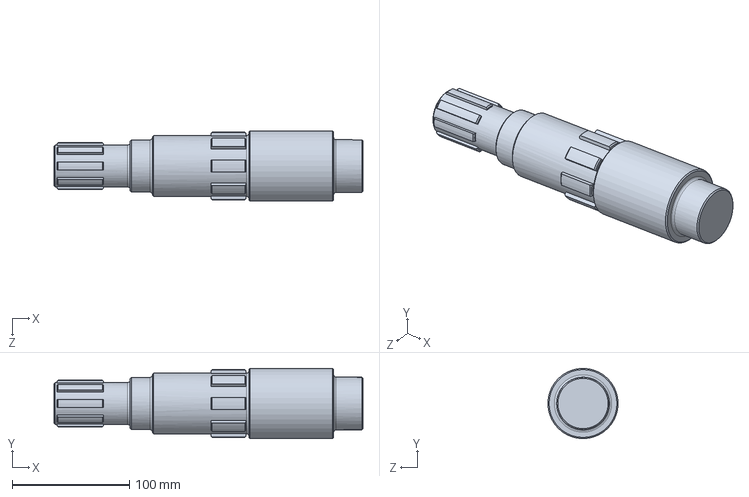
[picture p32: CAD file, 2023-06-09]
CAD_FINAL/CAD/Veio_4.SLDPRT
264.0 x 60.0 x 60.0 mm

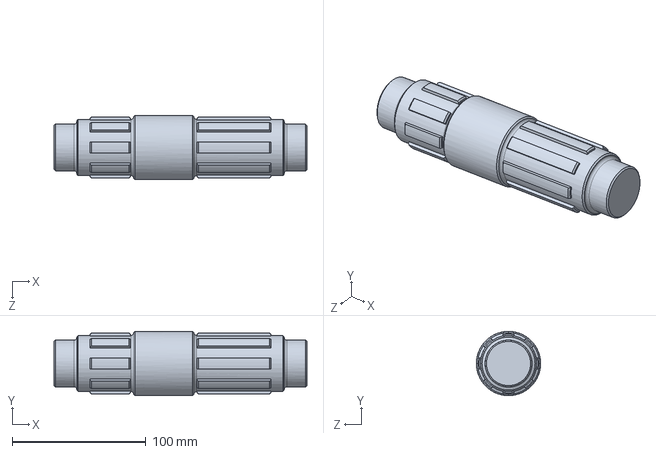
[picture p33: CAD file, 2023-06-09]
CAD_FINAL/CAD/Veio_2.SLDPRT
189.0 x 48.0 x 48.0 mm

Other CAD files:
CAD/Veio_3.SLDPRT
CAD/Veio_1.SLDPRT
CAD/Veio_4.SLDPRT
Veio_1.SLDPRT
Veio_3.SLDPRT
Veio_4.SLDPRT

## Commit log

2023-03-16 Pasta de PME
2023-03-17 Relatório de IMP Redutor cocentrico eixos paralelos
2023-03-18 Esta página de código é o fator de condução
2023-03-18 Código atualizado para as engrenagens V4
2023-04-21 Valores finais do tambor
    [pEM_p2.xlsx]
2023-04-30 veios de transmissão V1
2023-05-01 Versão atualizada do dimensionamento de veios
2023-05-03 Parte dos rolamentos feita mas a precisar de ser alterado para o ultimo veio
2023-05-07 Veio 1
    [Veio_1.SLDPRT]
2023-05-07 Veio 2
    [Veio_2.SLDPRT]
2023-05-07 Veio 3
    [Veio_3.SLDPRT]
2023-05-07 Veio 4
    [Veio_4.SLDPRT]
2023-05-07 relatório 2 de PME
2023-05-25 Valores atualizados das rodas para 900 rpm
2023-05-25 Motor novo - 900 rpm 60 hz
2023-05-29 Calculo de chavetas e veios estriados adicionados
2023-06-09 Pasta com elementeos em CAD
    [Veio_1.SLDPRT, Veio_2.SLDPRT, Veio_3.SLDPRT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]
2023-06-09 CAD final
    [Montagem_veio_1.SLDASM, Montagem_veio_2.SLDASM, Montagem_veio_3.SLDASM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]
